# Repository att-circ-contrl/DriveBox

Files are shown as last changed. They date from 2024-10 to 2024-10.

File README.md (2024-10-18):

# Triad Drive Motor Controller

## Overview

The Triad drive and its variants are driven by miniature motors from Namiki.
These take +/-3V sine waves with three phases and a common return
(probably Y-topology, but not ruling out delta-plus-ground).

The controller boxes we have are ones that we can't get more of, and the
cabling is unreliable, so I started designing a replacement.

**This was never finished.** A prototype of the front panel was designed
but the shield wasn't.

The tenatative plan was to use a 5V supply and use buffer amplifiers to
produce 0V, 2.5V, and 5V. The 2.5V line would be the common return, and
the motors would be driven with square waves at +/-2.5V.

There's no guarantee that this would have worked; the motors sometimes got
stuck even at 3V. But there's high confidence that it would be _safe_ to use
with the motors (de-rated voltage).

It's questionable if the AD86xx amplifiers would have been able to source
and sink enough current.

## Notes

The original plan was to have separate analog and digital headers, to avoid
injecting digital noise into the motor cabling (which is right next to ephys
cabling).

The revised plan (at least for the prototype) was to put the analog
circuitry on the mainboard (Arduino shield), and have analog and control
signals both on the microcontroller header.

The microcontroller header therefore has two different use-cases for the
same pinout. In digital mode, per the schematic, the "motor drive phase"
signals are driven at TTL voltages and the "Com/NC" signal is disconnected
(or better yet, grounded). In analog mode, the analog buffers are before
that header, and the "motor drive phase" signals are fed directly to the
motors, with "Com/NC" being the common return (shared between all motors,
which may cause problems with ground loops).

_(This is the end of the file.)_

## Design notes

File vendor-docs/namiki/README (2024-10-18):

Kevin used the SBL04 motors from Namiki for the Triad drives.
These are no longer manufactured. He has a small number of spares.
The datasheet is for the SBL07 through SBL12 motors.
These are three-phase stepper motors, it looks like.

Update:
Kevin says they're brushless DC motors, not steppers. The UVW inputs take
sine waves 120 degrees out of phase from each other, with the phase order
determining the motor directions, at +/- 3V.

Further update (18 March 2021):

The datasheet lists U, V, W, and common connections to the motor ribbon flex,
in the order "W", "com", "U", "V". Kevin soldered these in the opposite order
(W,c,U,V looking at the dark side of the flex rather than the copper side).
He also left "common" unconnected on the ribbon and wrapped the cable's
shielding braid around the motor housings instead.

Since the drives worked, I'll assume the datasheet's drawing was misleading
and that the motor coils are delta-connected rather than wye-connected.

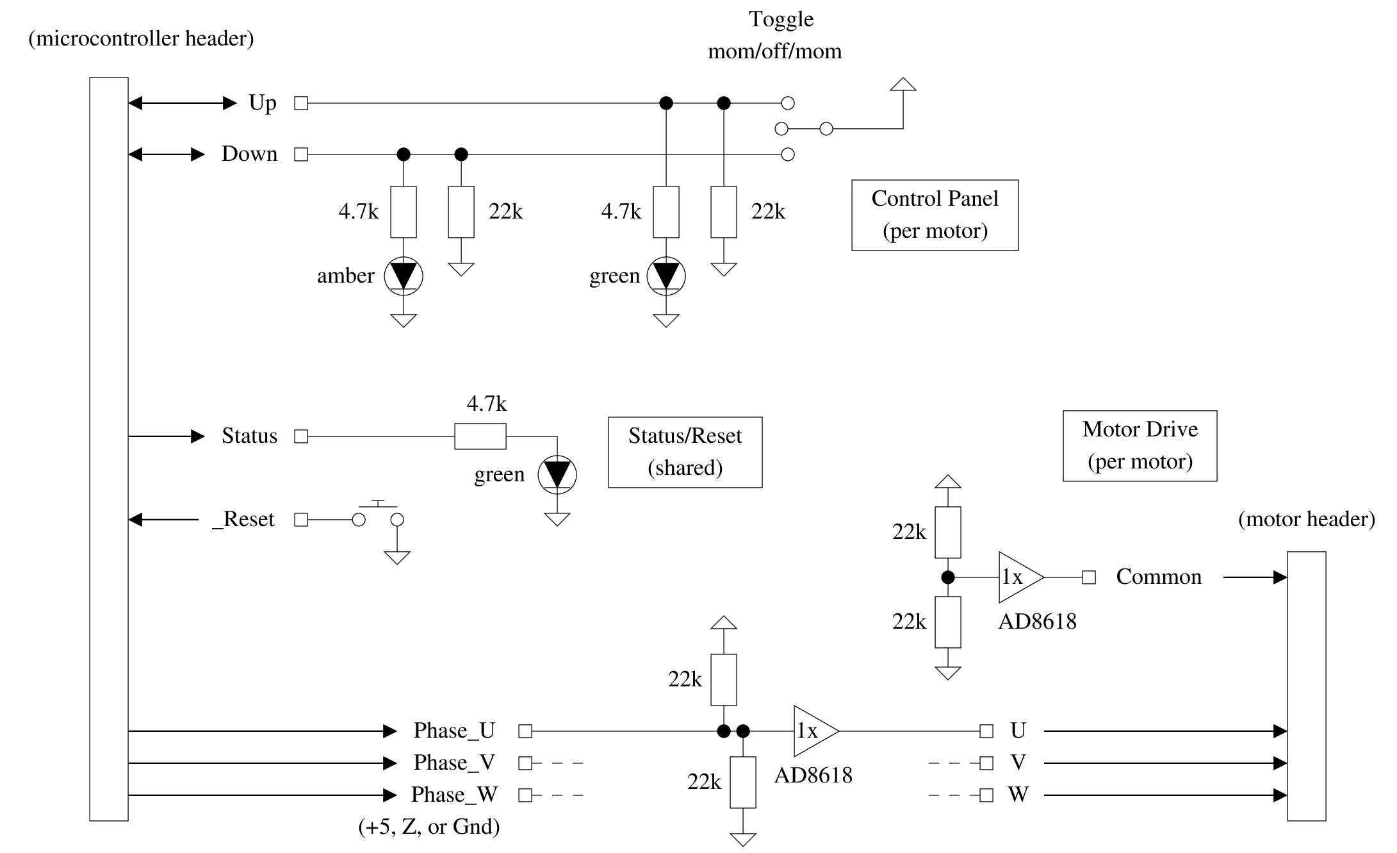
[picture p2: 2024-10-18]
panel-3up/schematics/panel-3up-schem.png

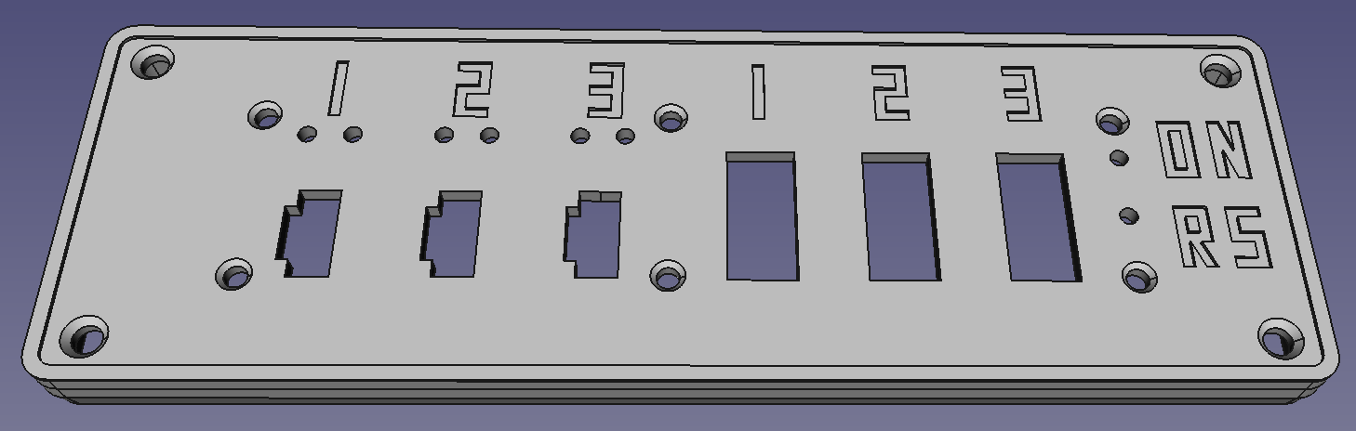
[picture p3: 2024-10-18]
panel-3up/mech/renders/panel-3up-faceplate-rc1.png

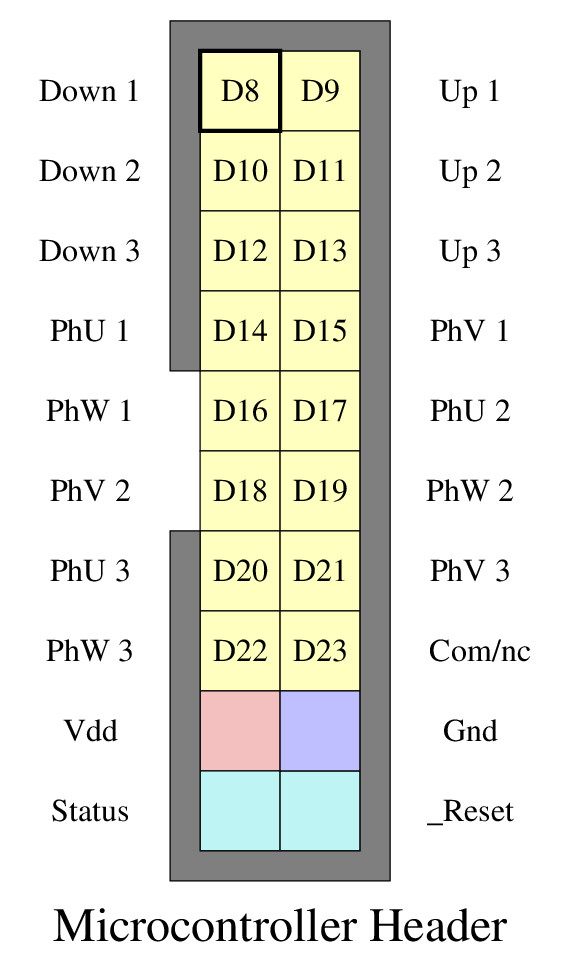
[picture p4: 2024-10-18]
panel-3up/diagrams/header-microcontroller.png

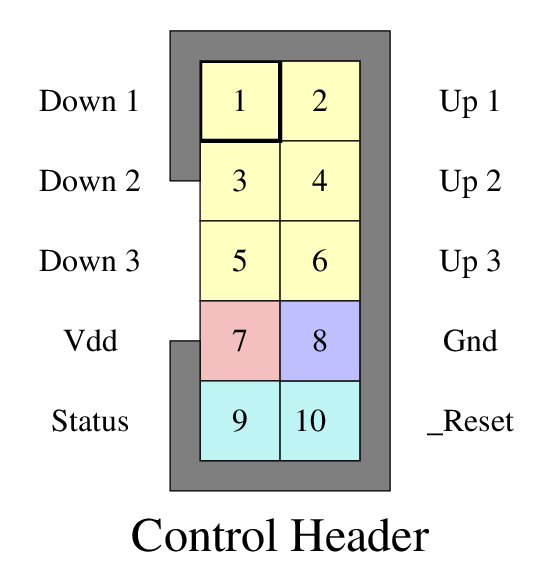
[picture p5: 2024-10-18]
panel-3up/diagrams/header-digctl.png

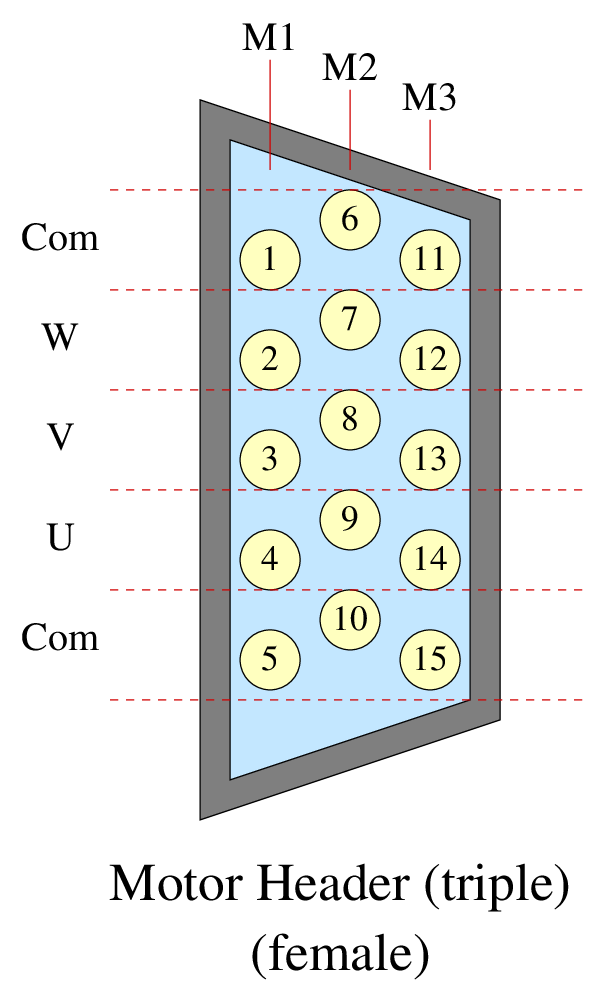
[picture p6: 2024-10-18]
panel-3up/diagrams/header-motor-vga-female.png

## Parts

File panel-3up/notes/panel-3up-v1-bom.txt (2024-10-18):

Item                                      Digikey p/n         Qty

VGA connecter vert with screw lock        609-4031-ND           1
rect conn fem 4pos latch and board lock   WM12790-ND            3
toggle switch mom-off-mom spdt            EG4563-ND             3

quad op-amp AD8618 soic                   AD8618ARZ-ND          3

resistor 0805 22 kohm                     311-22.0KCRCT-ND     30

header male 2x10 shr                      S9172-ND              1

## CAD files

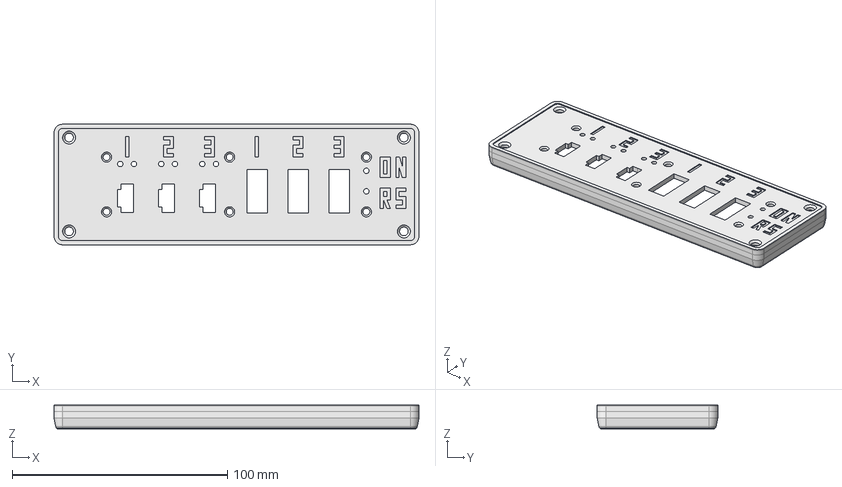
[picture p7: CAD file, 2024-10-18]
panel-3up/mech/motorbox-3up-plates.FCStd
169.5 x 56.0 x 11.0 mm

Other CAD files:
panel-3up/mech/faceplate-hm904.fcstd
panel-3up/mech/iges/faceplate-hm904-blank.iges
panel-3up/mech/meshes/faceplate-hm904-blank.stl
